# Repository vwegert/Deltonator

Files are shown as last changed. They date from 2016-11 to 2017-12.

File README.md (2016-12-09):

# CAUTION - WORK IN PROGRESS

If you happen to read this, beware - this has not been validated or tried out yet. So far, it is only a theoretical model.

# The Deltonator

You might also call it YAFDP - yet another f-word delta printer. It's a machine based on the linear delta kinematic
system like the famous [Rostock](http://reprap.org/wiki/Rostock) or [Kossel](http://reprap.org/wiki/Kossel). 

<a href="http://www.youtube.com/watch?feature=player_embedded&v=K8tiYmS-2c0" target="_blank">Deltonator Movement Simulation</a>

## Design Goals

When  setting out to build my own delta printer, I didn't find exactly what I was looking for, so - like many other 
people, many of which have considerable more experience than I have - I decided to design my own version, with the 
following design goals in mind:

 * Use the [MakerSlide](https://www.inventables.com/technologies/makerslide) system with V-shaped wheels for the 
   vertical axes.
 * Use a magnetic bearing system somewhat similar to the one designed by [Bert Broeren](http://www.thingiverse.com/thing:1239984), 
   that is, the magnets do not have to hold the weight of the effector.
 * Keep the effectors easily exchangeable to support different tool heads - various 3D printing heads, maybe a small 
   motor for PCB milling or a laser engraving module at some time.
 * Create an enclosed build volumes - for stable printing conditions, to prevent chips from flying all over the place 
   when milling and to contain the fumes when laser engraving.
 * Create a parametric design to be able to determine (and change) the sizes of key parts later on.
 * Keep the entire design open source, and use FOSS wherever possible.

At the current stage, the plans are incomplete and unproven, and any input is welcome. 

## OpenSCAD coding conventions

* global constants in UPPERCASE
* modules and functions lower_case_with_underscores
* things that are intended to be kept local begin with an _underscore

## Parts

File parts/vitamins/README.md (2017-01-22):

# Vitamins

This directory contains the files that produce parts that will have to be bought ready-made to prepare the printer.

## Bearings

Some of the bearings come from an extended version of the MCAD library, others are pre-generated from local 
instructions.

## GT2 pulleys

## Nuts

## Screws

The screws are pre-generated using the nutsnbolts library. Since that library (or any library) might not stay stable,
the repository contains the pre-rendered STL files.

## Stepper Motors

The motors are pre-generated using the MCAD library. Since that library (or any library) might not stay stable,
the repository contains the pre-rendered STL files.

## Switches

The SS-5GL switch model was downloaded from the [Omron Web Site](https://www.omron.com/ecb/products/sw/12/ss.html) and
then converted from STEP to STL manually using FreeCAD.

## V-Wheel

The file vwheel_b17021_rev_3.pdf was downloaded directly from the 
[buildlog site](http://www.buildlog.net/documents/b17021_rev_3.pdf). As far as I can tell from the PDF file, this file
has been licensed under a CC-BY-SA-3.0 license, but I have not been able to determine the actual author. Please 
contact me if you have details.

## Washers

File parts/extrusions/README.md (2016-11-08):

# Extrusions

This directory contains the files that are necessary to preoduce the extruded parts that are used for the printer frame.

## MakerSlide 

### own source files

* makerslide.scad contains some general functions that provide the dimensions of the profile as well as the modules used to import the rendered rails. This file is intended to be included by other files down the line.
* makerslide_rail.scad is used to render the actual rail into an STL file for faster access. This file is NOT intended to be included by any other file than makerslide.scad.

### files imported from external sources

Files:
* makerslide_b17022.dxf (original file name: b17022.dxf)
* makerslide_b17022_rev_2.pdf (original file name: b17022_rev_2.pdf)

These files were downloaded from [this repository](https://workbench.grabcad.com/workbench/projects/gcq_crZz-TsvjDvMKhmbtlfzNRmpeNJLO8d-8o69N-S1JA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), which in turn was linked from [the Inventables site](https://www.inventables.com/technologies/makerslide). As far as I can tell from the PDF file, these files have been licensed under a CC-BY-SA-3.0 license, but I have not been able to determine the actual author. Please contact me if you have details.

Files: 
* makerslide_extrusion_profile.dxf

Since the original extrusion profile was using non-standard dimensions and contained a considerable offset, I'm actually using a version by [mesheldrake](http://www.thingiverse.com/mesheldrake) downloaded from [Thingiverse](http://www.thingiverse.com/thing:8992). This file has been placed under a CC-BY-SA-3.0 license as well.

## OpenBuilds V-Slot 20x20 mm

### own source files

* vslot_2020.scad contains some general functions that provide the dimensions of the profile as well as the modules used to import the rendered rails. This file is intended to be included by other files down the line.
* vslot_2020_side.scad is used to render the actual side extrusion into an STL file for faster access. This file is NOT intended to be included by any other file than vslot_2020.scad.

### file simported from external sources

Files: 
* vslot_2020_fullscale.dxf (original file name: V-slot_2020_fullscale.dxd)

These files were downloaded from [the OpenBuilds website](http://www.openbuilds.com/projectresources/v-slot-extrusion-20x20-dxf.64/).

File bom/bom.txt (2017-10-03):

===== Aluminium Extrusions ============================================================

90° Corner Bracket for 2020 Extrusions
  ................................................................................ 6
    horizontal_assembly                                                      (6)

MakerSlide Extrusion
  800 mm.......................................................................... 3
    vertical_axis_assembly                                                   (3)

V-Slot Extrusion
  400x20x20 mm.................................................................... 9
    horizontal_assembly                                                      (9)

===== Bearings and Wheels =============================================================

Ball Bearing
  625RS........................................................................... 18
    vertical_axis_assembly >> carriage_hardware >> vslot_wheel               (18)
  F623............................................................................ 6
    vertical_axis_assembly >> tensioner_hardware                             (6)

Eccentric Spacer for V-Wheel
  ................................................................................ 3
    vertical_axis_assembly >> carriage_hardware                              (3)

V-Wheel for MakerSlide
  ................................................................................ 9
    vertical_axis_assembly >> carriage_hardware                              (9)

===== Electronic Components ===========================================================

Axial Fan
  25x25x10 mm..................................................................... 2
    effector_e3d_v6lite_hardware                                             (2)

End Switch
  SS-5GL.......................................................................... 3
    vertical_axis_assembly >> end_switch_bracket_hardware                    (3)

Escher IR Height Sensor
  Mini............................................................................ 1
    effector_e3d_v6lite_hardware >> ir_sensor_housing_hardware               (1)

Stepper Motor
  NEMA 17 medium.................................................................. 3
    vertical_axis_assembly >> motor_bracket_stepper                          (3)

===== General Hardware ================================================================

Flat Head Countersunk Socket Cap Screw (DIN 7991 / ISO 10642)
  M4 x 35 mm...................................................................... 3
    horizontal_assembly                                                      (3)

Hex Nut (DIN 934 / ISO 4032)
  M3.............................................................................. 6
    vertical_axis_assembly >> tensioner_hardware                             (6)
  M4.............................................................................. 21
    horizontal_assembly                                                      (6)
    horizontal_assembly >> enclosure_side_bracket_hardware                   (12)
    vertical_axis_assembly >> tensioner_hardware                             (3)
  M5.............................................................................. 9
    vertical_axis_assembly >> carriage_hardware                              (9)

Hex Socket Head Cap Screw (DIN 912 / ISO 4762)
  M2 x 10 mm...................................................................... 6
    vertical_axis_assembly >> end_switch_bracket_hardware >> screw           (6)
  M3 x 25 mm...................................................................... 3
    vertical_axis_assembly >> tensioner_hardware >> screw                    (3)
  M3 x 30 mm...................................................................... 3
    vertical_axis_assembly >> end_switch_bracket_hardware >> screw           (3)
  M3 x 6 mm....................................................................... 12
    vertical_axis_assembly >> motor_bracket_stepper_hardware >> screw        (12)
  M3 x 8 mm....................................................................... 8
    effector_e3d_v6lite_hardware >> ir_sensor_housing_hardware >> screw      (2)
    vertical_axis_assembly >> carriage_hardware >> screw                     (6)
  M4 x 10 mm...................................................................... 3
    horizontal_assembly >> screw                                             (3)
  M4 x 12 mm...................................................................... 48
    horizontal_assembly >> enclosure_side_bracket_hardware >> screw          (24)
    vertical_axis_assembly >> bed_bracket_hardware >> screw                  (6)
    vertical_axis_assembly >> foot_rail_hardware >> screw                    (6)
    vertical_axis_assembly >> head_hardware >> screw                         (6)
    vertical_axis_assembly >> motor_bracket_hardware >> screw                (6)
  M4 x 20 mm...................................................................... 30
    horizontal_assembly >> enclosure_long_side_plate_hardware >> screw       (12)
    vertical_axis_assembly >> enclosure_short_side_plate_hardware >> screw   (18)
  M4 x 25 mm...................................................................... 3
    vertical_axis_assembly >> tensioner_hardware >> screw                    (3)
  M4 x 8 mm....................................................................... 21
    horizontal_assembly >> screw                                             (3)
    vertical_axis_assembly >> bed_bracket_hardware >> screw                  (6)
    vertical_axis_assembly >> foot_rail_hardware >> screw                    (6)
    vertical_axis_assembly >> head_hardware >> screw                         (6)
  M5 x 25 mm...................................................................... 6
    vertical_axis_assembly >> carriage_hardware >> screw                     (6)
  M5 x 35 mm...................................................................... 3
    vertical_axis_assembly >> carriage_hardware >> screw                     (3)
  M8 x 30 mm...................................................................... 3
    vertical_axis_assembly >> foot_plate_hardware >> screw                   (3)

Large Washer (DIN 9021 / ISO 7093)
  M3.............................................................................. 6
    vertical_axis_assembly >> carriage_hardware                              (6)

Spring
  5x20 mm......................................................................... 6
    horizontal_assembly                                                      (3)
    vertical_axis_assembly >> end_switch_bracket_hardware                    (3)

T-Slot Nut
  M4.............................................................................. 75
    horizontal_assembly                                                      (3)
    horizontal_assembly >> enclosure_long_side_plate_hardware                (12)
    vertical_axis_assembly >> bed_bracket_hardware                           (12)
    vertical_axis_assembly >> enclosure_short_side_plate_hardware            (18)
    vertical_axis_assembly >> foot_rail_hardware                             (12)
    vertical_axis_assembly >> head_hardware                                  (12)
    vertical_axis_assembly >> motor_bracket_hardware                         (6)

Washer (DIN 125A / ISO 7089)
  M3.............................................................................. 30
    vertical_axis_assembly >> end_switch_bracket_hardware                    (3)
    vertical_axis_assembly >> motor_bracket_stepper_hardware                 (12)
    vertical_axis_assembly >> tensioner_hardware                             (15)
  M4.............................................................................. 117
    horizontal_assembly                                                      (18)
    horizontal_assembly >> enclosure_long_side_plate_hardware                (12)
    horizontal_assembly >> enclosure_side_bracket_hardware                   (24)
    vertical_axis_assembly >> bed_bracket_hardware                           (12)
    vertical_axis_assembly >> enclosure_short_side_plate_hardware            (18)
    vertical_axis_assembly >> foot_rail_hardware                             (12)
    vertical_axis_assembly >> head_hardware                                  (12)
    vertical_axis_assembly >> motor_bracket_hardware                         (6)
    vertical_axis_assembly >> tensioner_hardware                             (3)
  M5.............................................................................. 27
    vertical_axis_assembly >> carriage_hardware                              (27)

===== Printed Parts ===================================================================

Arm
  Carriage........................................................................ 3
    vertical_axis_assembly                                                   (3)

Effector
  E3D V6 Lite (Base Plate)........................................................ 1
                                                                             (1)
  E3D V6 Lite Spacer.............................................................. 2
    effector_e3d_v6lite_hardware                                             (2)

Enclosure
  Side Bracket.................................................................... 12
    horizontal_assembly                                                      (12)

Frame
  Bed Bracket..................................................................... 3
    vertical_axis_assembly                                                   (3)
  Foot (Rail Version)............................................................. 3
    vertical_axis_assembly                                                   (3)
  Foot Plate...................................................................... 3
    vertical_axis_assembly                                                   (3)
  Head............................................................................ 3
    vertical_axis_assembly                                                   (3)
  Motor Bracket................................................................... 3
    vertical_axis_assembly                                                   (3)

Small Parts
  Belt Tensioner.................................................................. 3
    vertical_axis_assembly                                                   (3)
  Bottom Magnet Holder............................................................ 6
    vertical_axis_assembly                                                   (6)
  End Switch Bracket.............................................................. 3
    vertical_axis_assembly                                                   (3)
  IR Sensor Housing............................................................... 1
    effector_e3d_v6lite_hardware                                             (1)
  Top Magnet Holder............................................................... 6
    vertical_axis_assembly                                                   (6)

===== Sheet / Cast Aluminium ==========================================================

Bed Plate
  d = 300 mm, h = 4 mm............................................................ 1
                                                                             (1)

===== Sheet / Multiplex Plywood =======================================================

Enclosure Door: Inner Horizontal Plate
  [3, 409, 56].................................................................... 2
    horizontal_assembly >> front_door_assembly                               (2)

Enclosure Door: Inner Vertical Plate
  [3, 29, 700].................................................................... 2
    horizontal_assembly >> front_door_assembly                               (2)

Enclosure Door: Outer Horizontal Plate
  [3, 320, 71.5].................................................................. 2
    horizontal_assembly >> front_door_assembly                               (2)

Enclosure Door: Outer Vertical Plate
  [3, 44.5, 813].................................................................. 2
    horizontal_assembly >> front_door_assembly                               (2)

Enclosure Long Side Plate
  411 x 800 x 6.5  mm............................................................. 2
    horizontal_assembly                                                      (2)

Enclosure Short Side Plate
  155 x 800 x 6.5  mm............................................................. 3
    vertical_axis_assembly                                                   (3)

===== Special Mechanic Parts ==========================================================

Carbon Fiber Rods
  330 mm, OD 8 mm, ID 0........................................................... 6
    vertical_axis_assembly                                                   (6)

Cylindrical Magnet
  d = 6 mm, h = 3 mm.............................................................. 2
    effector_e3d_v6lite_hardware >> ir_sensor_housing_hardware               (2)

Magnet Ring
  10x5 mm, bore 3.4 mm, 90° bevel with 7 mm diameter............................. 12
    vertical_axis_assembly >> magnet_holder_carriage_hardware                (6)
    vertical_axis_assembly >> magnet_holder_effector_hardware                (6)

Steel Ball
  10 mm diameter.................................................................. 12
    effector_e3d_v6lite_hardware >> effector_base_hardware                   (6)
    vertical_axis_assembly >> carriage_hardware                              (6)

===== Timing Belts and Pulleys ========================================================

GT2 Belt
  approx. 1504.82 mm.............................................................. 3
    vertical_axis_assembly                                                   (3)

GT2 Pulley
  20 Teeth x 5 mm Bore............................................................ 3
    vertical_axis_assembly >> motor_bracket_stepper                          (3)

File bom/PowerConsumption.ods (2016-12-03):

Pos. | Item |  | Current | Quantity | Combined
1 | Hotend Heater Cartridge | 40,0 W | 1,7 A | 3 | 5,0 A
2 | Extruder Stepper Motors |  | 0,2 A | 3 | 0,6 A
 | Rated Voltage | 2,55 V
 | Rated Current | 1,20 A
 | Additional Safety Factor | 50%
3 | Carriage Stepper Motors |  | 0,2 A | 3 | 0,6 A
 | Rated Voltage | 2,55 V
 | Rated Current | 1,20 A
 | Additional Safety Factor | 50%
4 | Extruder Fans | 4,0 W | 0,2 A | 2 | 0,3 A
5 | Part Cooling Fan | 6,0 W | 0,3 A | 1 | 0,3 A
6 | Electronics Fan | 5,0 W | 0,2 A | 2 | 0,4 A
7 | PanelDue | 3,5 W | 0,1 A | 1 | 0,1 A
8 | DuetWifi | 5,0 W | 0,2 A | 1 | 0,2 A
9
10
11
12
13
14
15
16
17
18
19
20
 | Subtotal |  |  |  | 7,5 A
 | Bed Heater | Diameter |  | 300 mm
 |  | Surface Area |  | 707 cm²
 |  | Power Factor |  | 0,4 W/cm²
 |  | Power |  | 282,7 W
 |  | Heater Current |  |  | 11,8 A
 | Spindle Motor |  | Power | 300,0 W
 |  |  | Motor Current |  | 12,5 A
 | Total Current |  |  |  | 20,0 A
 | Voltage |  | 24 V
 | Total Power |  |  |  |  | 480 W

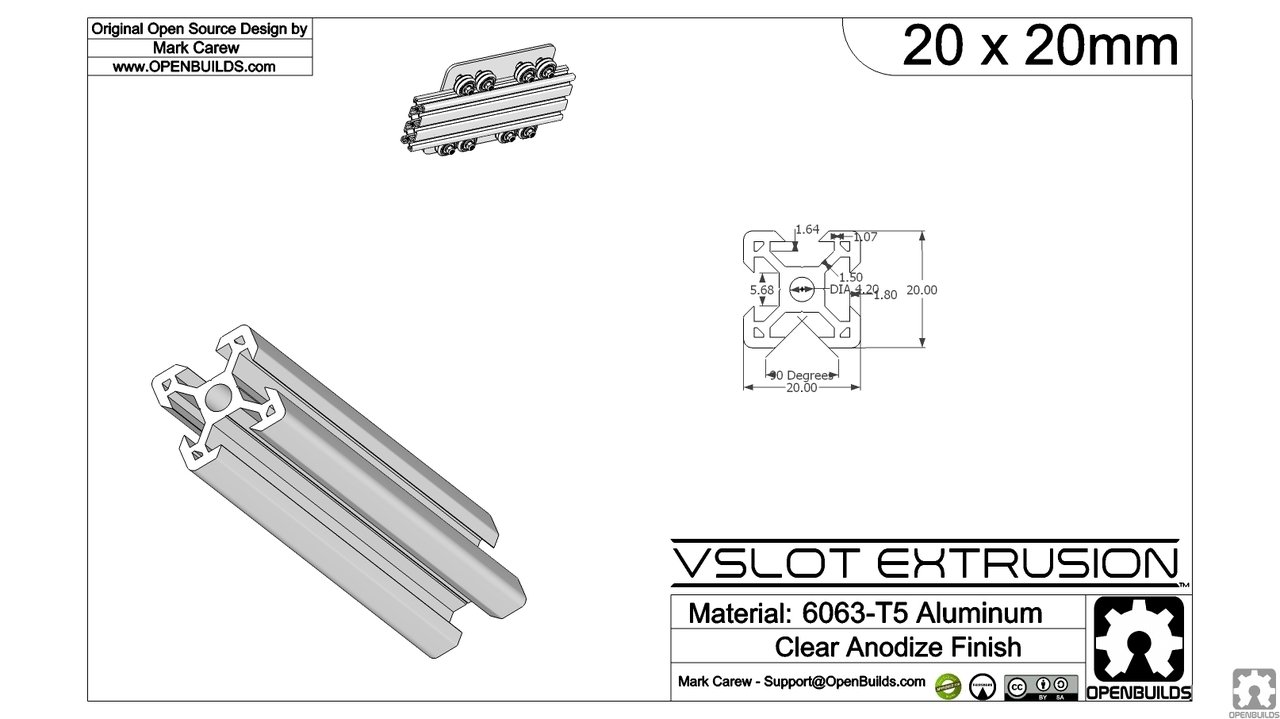
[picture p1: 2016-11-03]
parts/extrusions/vslot_2020_dimensions.jpg

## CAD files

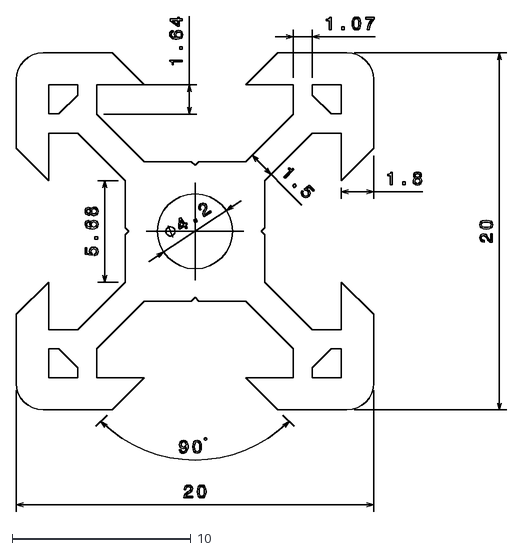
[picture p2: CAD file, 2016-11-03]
parts/extrusions/vslot_2020_fullscale.dxf
27.4 x 27.8

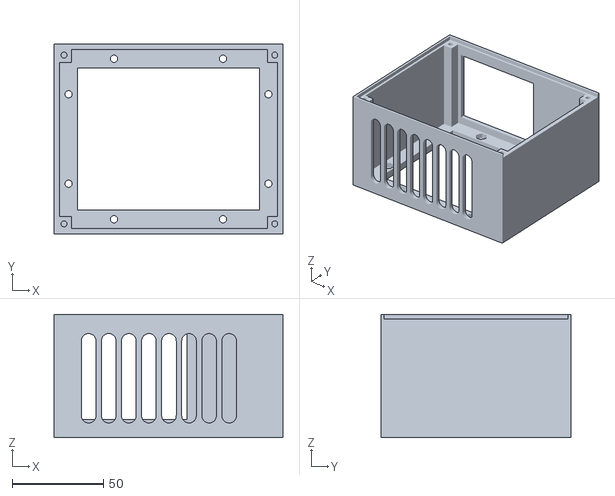
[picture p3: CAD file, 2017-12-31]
parts/printed/duet_holder.stl
125.5 x 104.0 x 67.5

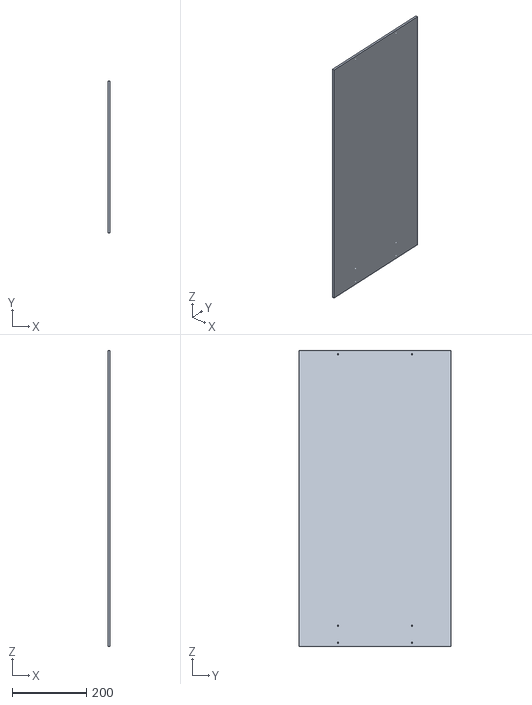
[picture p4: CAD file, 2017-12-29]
parts/sheets/enclosure_long_side.stl
6.50 x 411.0 x 800.0

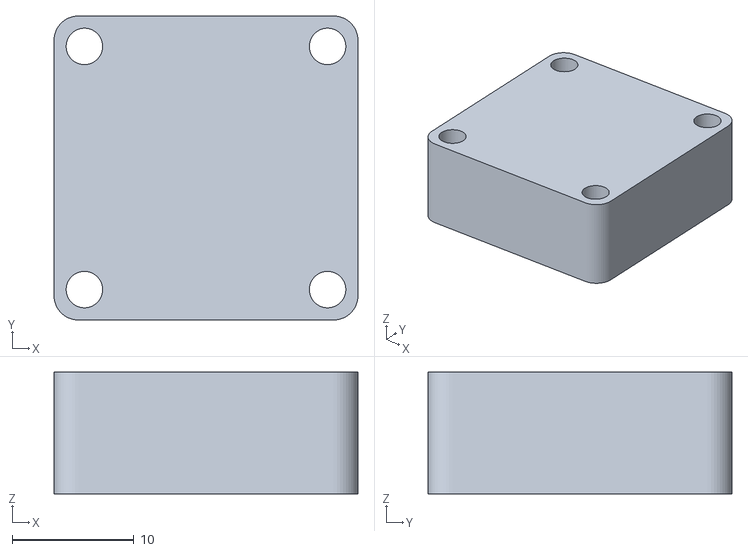
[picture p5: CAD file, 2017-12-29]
parts/vitamins/electromechanic/fan_axial_pc.stl
25.0 x 25.0 x 10.0

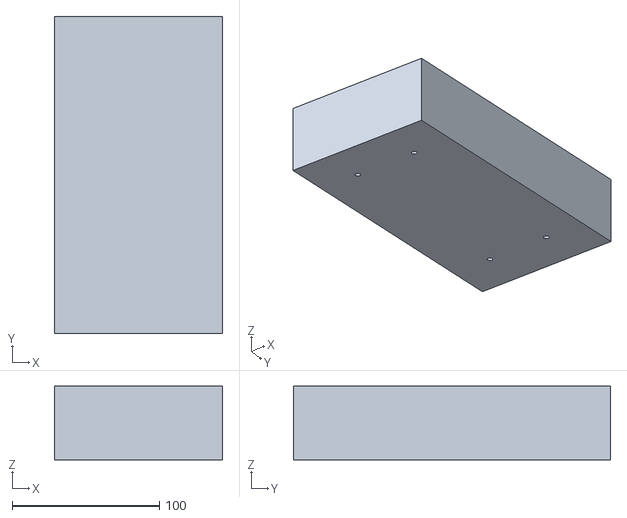
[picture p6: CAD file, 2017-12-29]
parts/vitamins/electronic/power_supply.stl
114.0 x 215.0 x 50.0

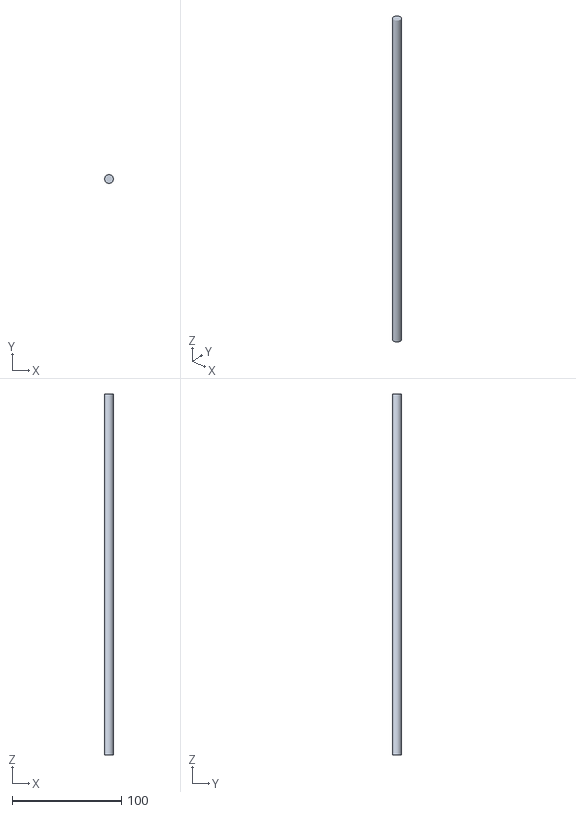
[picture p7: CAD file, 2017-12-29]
parts/vitamins/mechanic/rod.stl
8.00 x 8.00 x 330.0

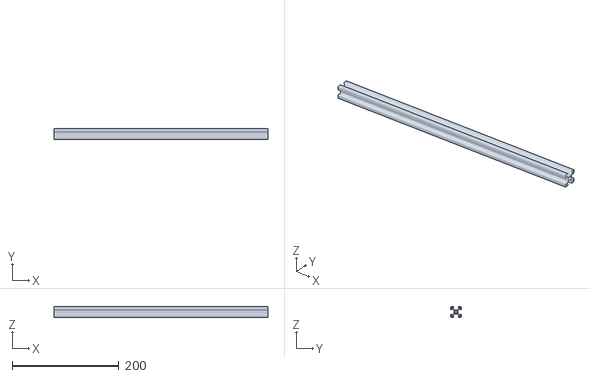
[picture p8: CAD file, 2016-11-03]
parts/extrusions/vslot_2020_side.stl
400.0 x 20.0 x 20.0

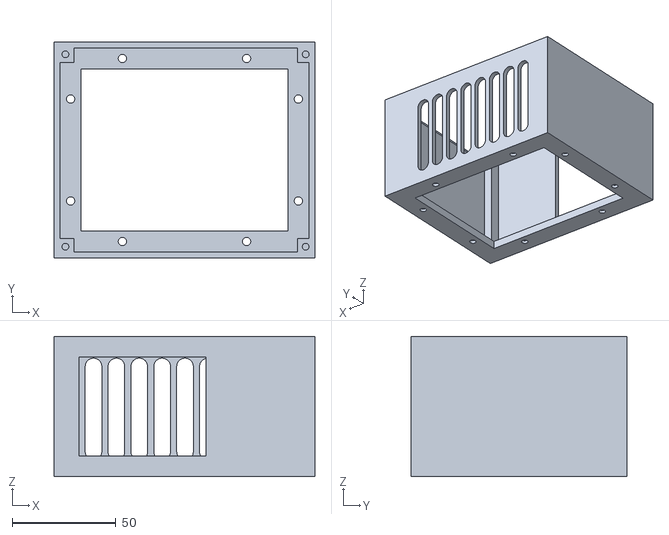
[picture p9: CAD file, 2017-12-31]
parts/printed/duetx_holder.stl
125.5 x 104.0 x 67.5

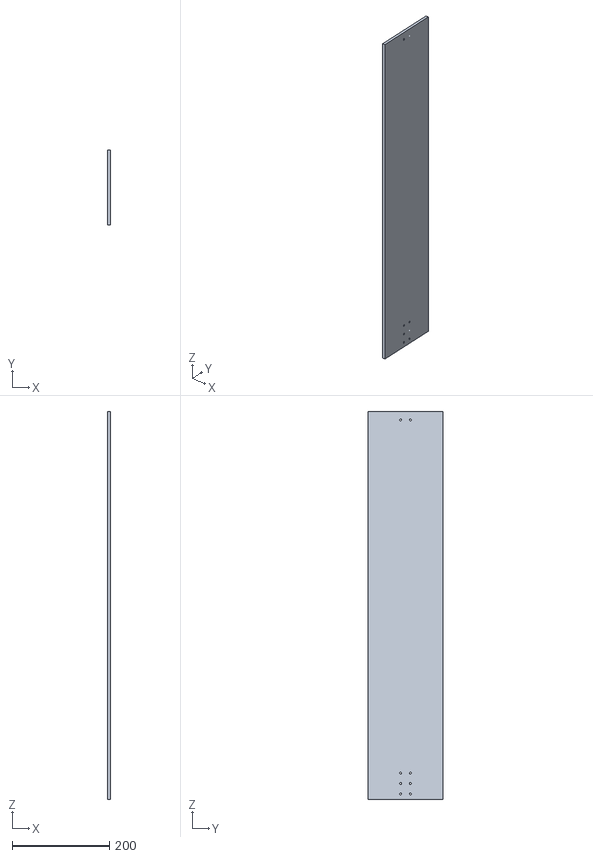
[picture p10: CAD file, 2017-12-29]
parts/sheets/enclosure_short_side.stl
6.50 x 155.0 x 800.0

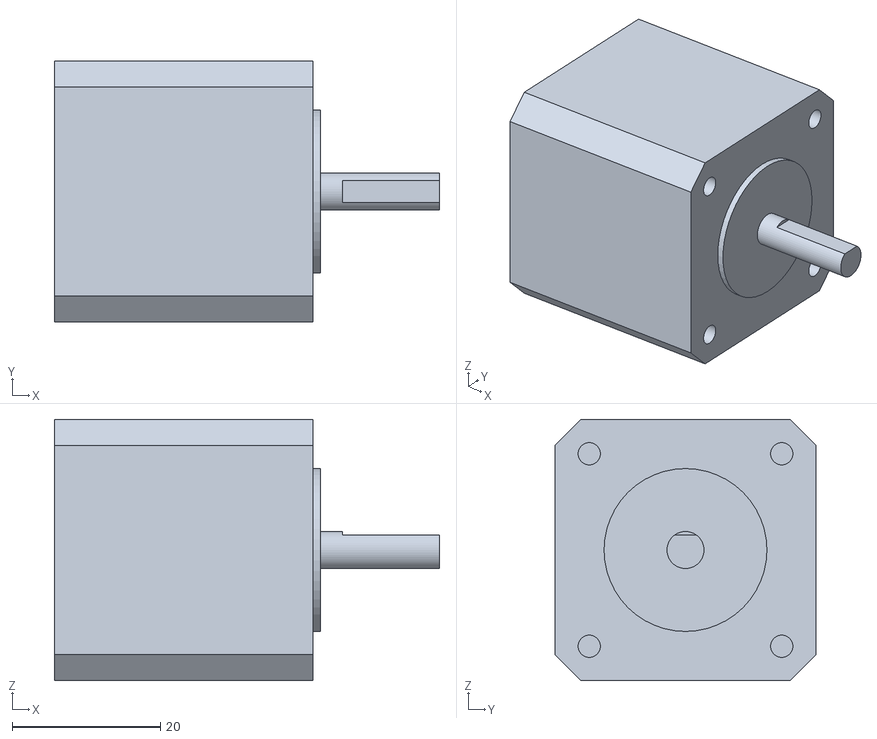
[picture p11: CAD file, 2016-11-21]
parts/vitamins/electromechanic/stepper_nema14_long.stl
52.0 x 35.3 x 35.3

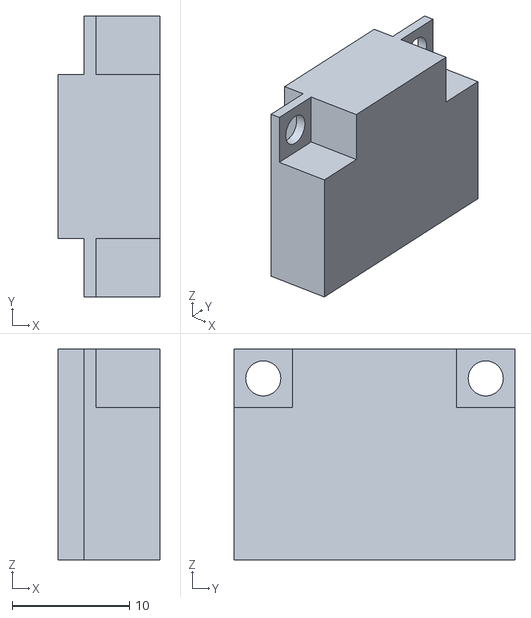
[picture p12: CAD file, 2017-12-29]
parts/vitamins/electronic/escher_ir_sensor.stl
8.75 x 24.0 x 18.0

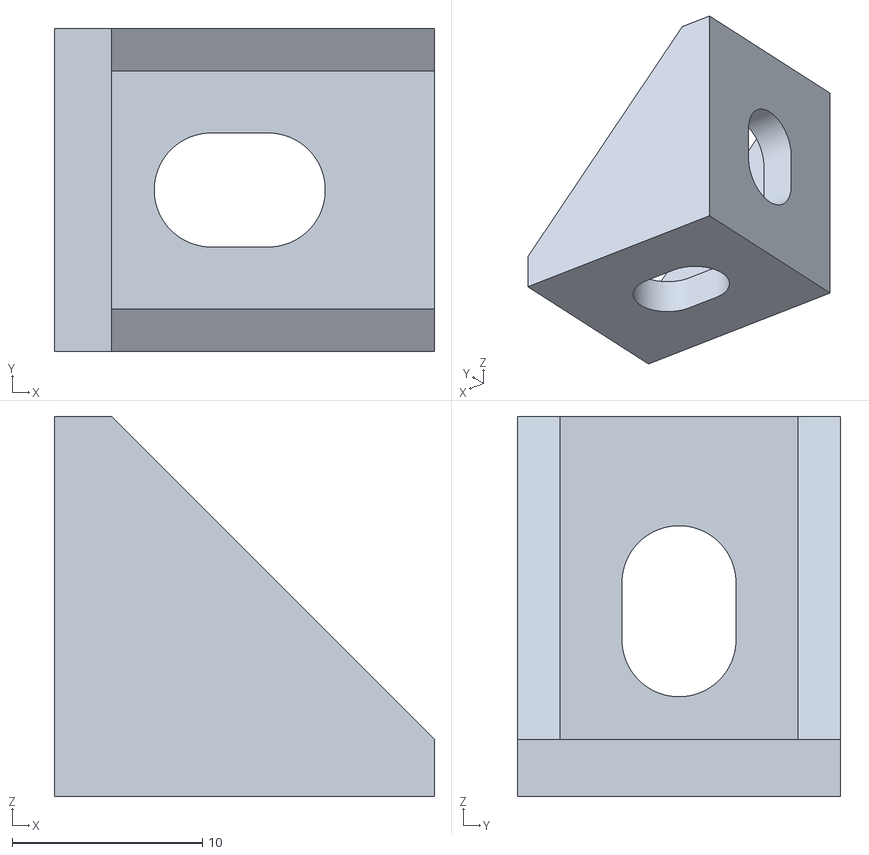
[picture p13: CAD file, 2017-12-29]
parts/vitamins/mechanic/rail_bracket.stl
20.0 x 17.0 x 20.0

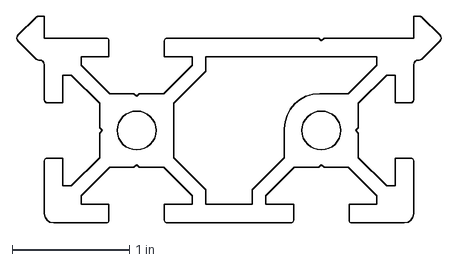
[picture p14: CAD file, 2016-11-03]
parts/extrusions/makerslide_b17022.dxf
3.62 x 1.76 in

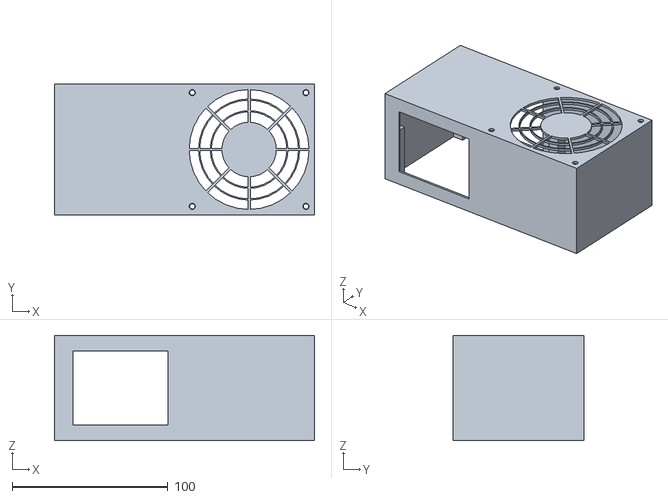
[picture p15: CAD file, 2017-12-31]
parts/printed/duet_fan_holder.stl
167.0 x 84.0 x 67.5

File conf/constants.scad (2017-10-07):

/**********************************************************************************************************************
 **
 ** conf/constants.scad
 **
 ** This file contains constants and aliases used for the part size definitions.
 **
 **********************************************************************************************************************/

/**
 * The alias names for the rails.
 * A is the "front left" rail, B the "front right" rail, C the back rail.
 * These constants are also used for the sides of the frame and the effector; in this case, side A is the one 
 * opposing rail A.
 */
A = 0;
B = 1;
C = 2;

/**
 * Aliases for metric screw/nut sizes.
 */
M2 = 2;
M3 = 3;
M4 = 4;
M5 = 5;
M8 = 8;

/** 
 * Aliases for NEMA stepper motors.
 */
NEMA14 = 14;
NEMA17 = 17;
NEMA23 = 23;

/**
 * The various types of effector heads supported.
 */
EFFECTOR_DUMMY      = 0;
EFFECTOR_E3D_V6LITE = 1;

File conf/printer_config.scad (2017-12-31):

/**********************************************************************************************************************
 **
 ** conf/printer_config.scad
 **
 ** This file contains the main control variables that determine the size and shape of the printer. Note that in the
 ** actual parts specifications, the constants defined here will only ever be accessed through functions defined in
 ** conf/derived_sizes.scad exclusively to allow for easier adaptation, should the mode of calculation change. 
 **
 ** All sizes in mm. Caution: Little to no cross-checking is implemented. Change values sensibly and one at a time.
 **
 ** This file is NOT to be included by any other file except for conf/derived_sizes.scad.
 **
 **********************************************************************************************************************/

include <constants.scad>

// ===== FRAME RAIL DIMENSIONS ========================================================================================

// The length of the vertical MakerSlide extrusions that make up the rails for the carriages.
FRAME_V_RAIL_HEIGHT = 800;

// The length of the horizontal 20x20 V-Slot extrusions that form the sides of the triangle.
FRAME_H_RAIL_LENGTH = 400;

// ===== WORKING SURFACE (BED) DIMENSIONS =============================================================================

// The thickness of the plate that serves as the heated bed.
BED_THICKNESS = 4;

// The diameter of the plate that serves as the heated bed.
BED_DIAMETER = 300;

// ===== DIMENSIONS OF THE PRINTED FRAME PARTS ========================================================================

// The additional clearance to leave around the MakerSlide extrusion.
MAKERSLIDE_CLEARANCE = 0.25;

// The thickness of the walls outside the extruded parts.
FRAME_PART_WALL_THICKNESS = 3;

// The thickness of the wall that separates the vertical rails from the horizontal extrusions.
FRAME_V_H_RAIL_SEPARATION = 8;

// The depth of the holes that hold the V-Slot extrusions.
FRAME_PART_VSLOT_DEPTH = 30;

// Whether to use a horizontal rail at the base of the printer or not.
FRAME_HORIZONTAL_BASE_RAIL = true;

// The depth of the holes in the foot that hold the MakerSlide extrusions. This is for the foot version that holds
// a horizontal rail.
FRAME_FOOT_RAIL_MAKERSLIDE_DEPTH = 23; 

// The depth of the plate in the foot that the external foot will screw into.
FRAME_FOOT_RAIL_PLATE_DEPTH = 15;

// The thickness of the plate in the foot that the external foot will screw into.
// Hint: Easier to print (although more material is required) if equals to FRAME_FOOT_RAIL_MAKERSLIDE_DEPTH.
FRAME_FOOT_RAIL_PLATE_HEIGHT = 23;

// The depth of the holes in the foot that hold the MakerSlide extrusions. This is for the foot version that does not
// hold a horizontal rail.
FRAME_FOOT_NORAIL_MAKERSLIDE_DEPTH = 17.5; 

// The size of the screws that can be used to mount the foot to the underlying surface.
FRAME_FOOT_PLATE_SCREW_SIZE = M8;

// The clearance to leave around the screw head on all sides.
FRAME_FOOT_PLATE_SCREW_HEAD_CLEARANCE = 0.25;

// The diameter of the adjustable foot that screws into the foot bracket. 
// Note that the polygon is INscribed into this circumference.
FRAME_FOOT_PLATE_DIAMETER = 50;

// The number of sides to the adjustable foot that screws into the foot bracket.
FRAME_FOOT_PLATE_SIDES = 8;

// The thickness of the adjustable foot that screws into the foot bracket.
// Keep this larger than the head of the screw used to fix it, or you will run into trouble.
FRAME_FOOT_PLATE_THICKNESS = 6.5;

// The height of the bracket that holds the motor. WARNING: Increasing this might make it difficult to 
// turn the screws that hold the motor.
FRAME_MOTOR_BRACKET_HEIGHT = 20;

// The height of the bracket that holds the intermediate level with the working surface (print bed).
// Will be A LOT easier to print if equals to 2020 extrusion width + FRAME_PART_WALL_THICKNESS
FRAME_BED_BRACKET_HEIGHT = 23; 

// The depth of the holes in the head that hold the MakerSlide extrusions.
FRAME_HEAD_MAKERSLIDE_DEPTH = 35; 

// The clearance between the tensioner / bracket and its guide blocks on either side.
FRAME_HEAD_GUIDE_CLEARANCE = 0.5;

// ===== ENCLOSURE DIMENSIONS =========================================================================================

// The material thickness of the solid (back and side) enclosure walls.
ENCLOSURE_SOLID_THICKNESS = 6.5;

// The thickness of the insulation layer between the enclosure walls and the brackets they are mounted to.
ENCLOSURE_INSULATION_THICKNESS = 2;

// The gap between the horizontal extrusions and the enclosure side walls.
ENCLOSURE_SIDE_GAP = 40;

// The factor used to round down the enclosure plate widths.
ENCLOSURE_ROUND_DOWN_TO = 1;

// The thickness of the brackets that hold the outer enclosure walls.
ENCLOSURE_BRACKET_THICKNESS = 6;

// The width of the brackets that hold the outer enclosure walls, excluding the parts that bolt on to the 
// horizontal rails.
ENCLOSURE_BRACKET_WIDTH = 40;

// The size of the glass pane in the front door.
ENCLOSURE_GLASS_WIDTH = 350;
ENCLOSURE_GLASS_HEIGHT = 700;

// The size of the gap around the glass pane.
ENCLOSURE_GLASS_GAP_WIDTH = 1.0;

// The width of the bevel in the front door that holds the glass.
ENCLOSURE_GLASS_BEVEL_WIDTH = 15;

// The additional clearance on the sides of the front door to allow for the hinge to move.
ENCLOSURE_DOOR_SIDE_CLEARANCE = 2.0;

// The thickness of the material of the front door.
ENCLOSURE_DOOR_WOOD_THICKNESS = 3.0;
ENCLOSURE_DOOR_GLASS_THICKNESS = 1.8;

// ===== CARRIAGE DIMENSIONS ==========================================================================================

// The thickness of the carriage base plate. A thicker plate will make the carriage stiffer, but cost more
// material to print and take away space from the working area.
CARRIAGE_PLATE_THICKNESS = 6;

// The width of the border around the holes in the carriage base plate that hold the V-Wheels. 
CARRIAGE_PLATE_BORDER_WIDTH = 8;

// The upward angle of the ball holder on the carriage.
CARRIAGE_BALL_HOLDER_ANGLE = 10;

// ===== ARM DIMENSIONS AND PARAMETERS ================================================================================

// The distance between the rods that hold the effector.
ROD_DISTANCE = 65;

// The outer diameter of the rods.
ROD_OUTER_DIAMETER = 8;

// The inner diameter of the rods. Set to 0 if the rods are not hollow.
ROD_INNER_DIAMETER = 0;

// The additional clearance to leave between the rod and the holder.
ROD_CLEARANCE = 0.25;

// The thickness of the outer wall around the rod.
ROD_HOLDER_WALL_THICKNESS = 2.2;

// The depth of the insets that hold the rods.
ROD_HOLDER_DEPTH = 10;

// The size of the text on the outside of the rod holders.
ROD_HOLDER_TEXT_SIZE = 9;

// The depth of the text on the outside of the rod holders.
ROD_HOLDER_TEXT_DEPTH = 0.5;

// The minimum angle of the arms.
ROD_MIN_ANGLE = 18;

// The factor used to round up the rod length.
ROD_ROUND_UP_TO = 5;

// Set this to a positive value if you want the rods to have a fixed length (for example if you have pre-fabricated
// rods). Set this to a negative value to have the rod length calculated automatically.
ROD_FIXED_LENGTH = 330;

// The thickness of the magnet holder arms.
MAGNET_HOLDER_THICKNESS = 5;

// The additional clearance to leave around the magnet holder pin.
MAGNET_CLEARANCE = 0.025;

// ===== IR SENSOR DIMENSIONS AND PARAMETERS ==========================================================================

// The additional clearance to leave around the PCB.
IR_SENSOR_PCB_CLEARANCE = 0.25;

// The additional clearance to leave around the magnets.
IR_SENSOR_MAGNET_CLEARANCE = 0.2;

// The size of the screws used to adjust the IR sensor.
IR_SENSOR_ADJUSTMENT_SCREW_SIZE = M4;

// ===== EFFECTOR DIMENSIONS AND PARAMETERS ===========================================================================

// The additional distance between the magnets on the effector (not the rod distance - the other one :-)).
// This value is added to the minimum distance determined by the magnet size and wall thickness.
EFFECTOR_BALL_ADDITIONAL_DISTANCE = 15;

// The thickness of the effector plate.
EFFECTOR_THICKNESS = 4;

// The type of effector to use.
EFFECTOR_TYPE = EFFECTOR_E3D_V6LITE;

// The clearance in Z direction to leave beneath the effector plate.
EFFECTOR_Z_CLEARANCE = 30.0;

// ===== POWER DISTRIBUTION PARAMETERS ================================================================================

// The thickness of the cover walls.
POWER_WALL_THICKNESS = 1.5;

// The clearance between the inner and outer parts of the covers as well as between the covers.
POWER_CLEARANCE = 0.5;

// ===== ELECTRONICS MOUNTING PARAMETERS ==============================================================================

// The thickness of the cover walls.
ELECTRONICS_WALL_THICKNESS = 1.5;
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

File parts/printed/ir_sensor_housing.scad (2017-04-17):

/**********************************************************************************************************************
 **
 ** parts/printed/ir_sensor_housing.scad
 **
 ** This file constructs the housing for the Mini Differential IR height sensor board available from 
 ** http://www.escher3d.com/pages/order/products/product1.php
 **
 **********************************************************************************************************************/

include <../../conf/colors.scad>
include <../../conf/derived_sizes.scad>
include <../../conf/part_sizes.scad>

use <../../bom/bom.scad>
use <../../parts/vitamins/vitamins.scad>

/**
 * Renders the main body of the housing without the "wings" to fasten it.
 */
module _ir_sensor_housing_body() {

	difference() {
		union() {
			// the outer shape of the housing
			difference() {
				cube([escher_ir_sensor_housing_body_depth(),
					  escher_ir_sensor_housing_body_width(),
					  escher_ir_sensor_housing_body_height()]);
				translate([escher_ir_sensor_housing_wall_thickness(), escher_ir_sensor_housing_wall_thickness(), 0])
				cube([escher_ir_sensor_housing_body_depth() - 2 * escher_ir_sensor_housing_wall_thickness(),
					  escher_ir_sensor_housing_body_width() - 2 * escher_ir_sensor_housing_wall_thickness(),
					  escher_ir_sensor_housing_body_height()]);
			}
		
			// the "resting blocks" on the underside of the PCB
			translate([escher_ir_sensor_housing_wall_thickness(), 
				       escher_ir_sensor_housing_wall_thickness(), 
				       0])
				cube([escher_ir_sensor_housing_top_bottom_clearance() + escher_ir_sensor_pcb_max_pin_length(),
					  escher_ir_sensor_pcb_bottom_side_clearance(),
					  escher_ir_sensor_housing_body_height()]);
			translate([escher_ir_sensor_housing_wall_thickness(), 
				       escher_ir_sensor_housing_body_width() - escher_ir_sensor_housing_wall_thickness() - escher_ir_sensor_pcb_bottom_side_clearance(), 
				       0])
				cube([escher_ir_sensor_housing_top_bottom_clearance() + escher_ir_sensor_pcb_max_pin_length(),
					  escher_ir_sensor_pcb_bottom_side_clearance(),
					  escher_ir_sensor_housing_body_height()]);
		
			// the "mounting blocks" on the component side of the PCB
			_mounting_block_thickness = escher_ir_sensor_pcb_max_component_height() + 
			                            escher_ir_sensor_housing_top_bottom_clearance();
			_mounting_block_x_offset = escher_ir_sensor_housing_body_depth() - escher_ir_sensor_housing_wall_thickness() - _mounting_block_thickness;
			_mounting_block_height = escher_ir_sensor_housing_body_height() - ( escher_ir_sensor_pcb_height() - escher_ir_sensor_pcb_top_edge_clearance() );
			_mounting_block_z_offset = escher_ir_sensor_pcb_height() - escher_ir_sensor_pcb_top_edge_clearance();
			translate([_mounting_block_x_offset, 
				       escher_ir_sensor_housing_wall_thickness(), 
				       _mounting_block_z_offset])
				cube([_mounting_block_thickness,
					  escher_ir_sensor_pcb_top_edge_clearance(),
					  _mounting_block_height]);
			translate([_mounting_block_x_offset, 
					   escher_ir_sensor_housing_body_width() - escher_ir_sensor_housing_wall_thickness() - escher_ir_sensor_pcb_top_edge_clearance(), 
				       _mounting_block_z_offset])
				cube([_mounting_block_thickness,
					  escher_ir_sensor_pcb_top_edge_clearance(),
					  _mounting_block_height]);
		}

		// minus the screw holes
		translate([-epsilon(),
			       escher_ir_sensor_screw_y_offset(),
			       escher_ir_sensor_screw_z_offset()])
			rotate([0, 90, 0])
				cylinder(d = tap_base_diameter(escher_ir_sensor_hole_size()),
					     h = escher_ir_sensor_housing_body_depth() + 2 * epsilon(),
				    	 $fn = escher_ir_sensor_resolution());
		translate([-epsilon(),
			       escher_ir_sensor_housing_body_width() - escher_ir_sensor_screw_y_offset(),
			       escher_ir_sensor_screw_z_offset()])
			rotate([0, 90, 0])
				cylinder(d = tap_base_diameter(escher_ir_sensor_hole_size()),
					     h = escher_ir_sensor_housing_body_depth() + 2 * epsilon(),
				    	 $fn = escher_ir_sensor_resolution());
	}
}

/**
 * Renders the two "wings" that hold the magnets.
 */
module _ir_sensor_housing_magnet_holders() {

	// move to the Z base
	translate([0, 0, escher_ir_sensor_housing_body_height() - escher_ir_sensor_magnet_holder_height()]) {

		// create the left block
		translate([0, -escher_ir_sensor_magnet_holder_width(), 0]) 
			difference() {
				// the block
				cube([escher_ir_sensor_magnet_holder_depth(),
					  escher_ir_sensor_magnet_holder_width(),
					  escher_ir_sensor_magnet_holder_height()]);

				// minus the hole for the magnets
				translate([escher_ir_sensor_magnet_holder_depth() / 2,
					       escher_ir_sensor_housing_wall_thickness() + escher_ir_sensor_magnet_clearance() + escher_ir_sensor_magnet_diameter()/2,
					       escher_ir_sensor_magnet_holder_height() - (escher_ir_sensor_magnet_height() + escher_ir_sensor_magnet_clearance())])
				cylinder(d = escher_ir_sensor_magnet_diameter() + 2 * escher_ir_sensor_magnet_clearance(),
					     h = escher_ir_sensor_magnet_height() + escher_ir_sensor_magnet_clearance(),
					     $fn = escher_ir_sensor_resolution());
			}

		// create the right block
		translate([0, escher_ir_sensor_housing_body_width(), 0]) 
			difference() {
				// the block
				cube([escher_ir_sensor_magnet_holder_depth(),
					  escher_ir_sensor_magnet_holder_width(),
					  escher_ir_sensor_magnet_holder_height()]);

				// minus the hole for the magnets
				translate([escher_ir_sensor_magnet_holder_depth() / 2,
					       escher_ir_sensor_magnet_clearance() + escher_ir_sensor_magnet_diameter()/2,
					       escher_ir_sensor_magnet_holder_height() - (escher_ir_sensor_magnet_height() + escher_ir_sensor_magnet_clearance())])
				cylinder(d = escher_ir_sensor_magnet_diameter() + 2 * escher_ir_sensor_magnet_clearance(),
					     h = escher_ir_sensor_magnet_height() + escher_ir_sensor_magnet_clearance(),
					     $fn = escher_ir_sensor_resolution());
			}
	}
} 

/**
 * Creates the housing by rendering it from scratch. This module is not to be called externally, use 
 * ir_sensor_housing() instead.
 */
module _render_ir_sensor_housing() {
	color_printed_head_parts()
		render() {
			translate([-escher_ir_sensor_housing_body_depth() / 2,
				       -escher_ir_sensor_housing_body_width() / 2,
				       -escher_ir_sensor_housing_body_height()]) {
				_ir_sensor_housing_body();
				_ir_sensor_housing_magnet_holders();
			}
		} 
}

/**
 * Main module to use the pre-rendered sensor housing. 
 * The housing is centered on its base to facilitate mounting calculations.
 */
module ir_sensor_housing() {
	bom_entry(section = "Printed Parts", description = "Small Parts", size = "IR Sensor Housing");
	color_printed_head_parts()
		import(file = "ir_sensor_housing.stl");
}

/** 
 * Renders the hardware (nuts, bolts, screws) that are used to fixed the printed part to the surrounding parts.
 * This also includes the sensor board.
 */
module ir_sensor_housing_hardware() {

	translate([-escher_ir_sensor_housing_body_depth() / 2,
		       -escher_ir_sensor_housing_body_width() / 2,
		       -escher_ir_sensor_housing_body_height()]) {

		// the sensor board inside the housing
		translate([escher_ir_sensor_housing_wall_thickness() 
			       + escher_ir_sensor_housing_top_bottom_clearance()
    	           + escher_ir_sensor_pcb_max_pin_length()
    	           + escher_ir_sensor_housing_pcb_clearance(),
			       escher_ir_sensor_housing_wall_thickness() 
    	           + escher_ir_sensor_housing_pcb_clearance(),
			       0])
			escher_ir_sensor();
	
		// the screws to hold the sensor board
		translate([-epsilon(),
			       escher_ir_sensor_screw_y_offset(),
			       escher_ir_sensor_screw_z_offset()])
			screw(size = escher_ir_sensor_hole_size(),
				  min_length = escher_ir_sensor_screw_min_length(),
				  max_length = escher_ir_sensor_housing_body_depth());
		translate([-epsilon(),
			       escher_ir_sensor_housing_body_width() - escher_ir_sensor_screw_y_offset(),
			       escher_ir_sensor_screw_z_offset()])
			screw(size = escher_ir_sensor_hole_size(),
				  min_length = escher_ir_sensor_screw_min_length(),
				  max_length = escher_ir_sensor_housing_body_depth());
	
		// the magnets
		translate([escher_ir_sensor_magnet_holder_depth()/2,
			       - escher_ir_sensor_magnet_diameter() / 2 - escher_ir_sensor_magnet_clearance(), 
			       escher_ir_sensor_housing_body_height() - escher_ir_sensor_magnet_height()]) 
			magnet_cylinder();
		translate([escher_ir_sensor_magnet_holder_depth()/2,
			       escher_ir_sensor_housing_body_width() + escher_ir_sensor_magnet_diameter() / 2 + escher_ir_sensor_magnet_clearance(), 
			       escher_ir_sensor_housing_body_height() - escher_ir_sensor_magnet_height()]) 
			magnet_cylinder();

	}
}

_render_ir_sensor_housing();

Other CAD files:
parts/sheets/bed.stl
parts/vitamins/electromechanic/stepper_nema17_short.stl
parts/vitamins/electronic/duet_wifi_board.stl
parts/vitamins/mechanic/magnet_cylinder.stl
parts/printed/motor_bracket.scad
assemblies/extruder_plate.scad
assemblies/front_door.scad
assemblies/horizontal_right.scad
assemblies/horizontal_side.scad
assemblies/vertical_axis.scad
bom/bom.scad
conf/colors.scad
conf/derived_sizes.scad
conf/part_sizes.scad
parts/extrusions/makerslide.scad
parts/extrusions/makerslide_extrusion_profile.dxf
parts/extrusions/makerslide_rail.scad
parts/extrusions/makerslide_rail.stl
parts/extrusions/vslot_2020.scad
parts/extrusions/vslot_2020_side.scad
parts/printed/bed_bracket.scad
parts/printed/bed_bracket.stl
parts/printed/carriage.scad
parts/printed/carriage.stl
parts/printed/duet_common.scad
parts/printed/duet_fan_holder.scad
parts/printed/duet_holder.scad
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

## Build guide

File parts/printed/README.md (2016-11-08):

# Printed Parts

This directory contains the files that produce the parts that need to be printed (or IM'ed if thousands of orders 
should be placed, haha).

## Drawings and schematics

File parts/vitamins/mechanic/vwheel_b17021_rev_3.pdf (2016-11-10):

| REVISIONS

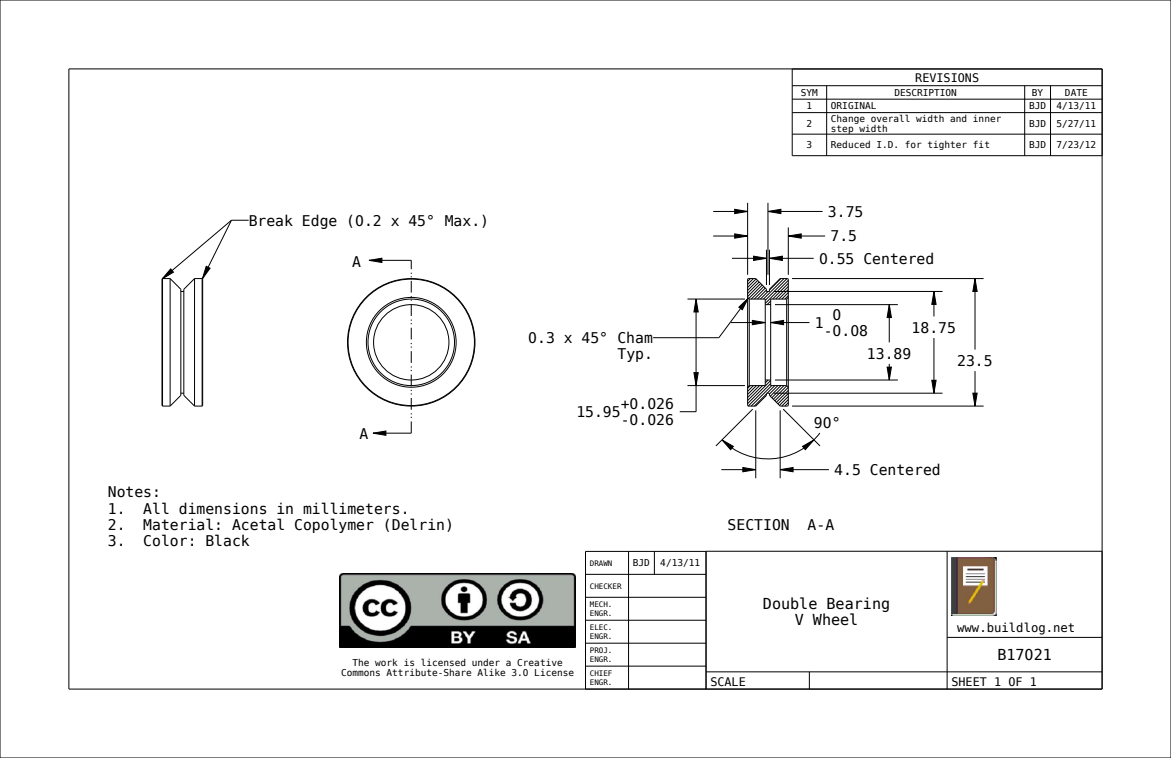
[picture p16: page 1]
0.55 Centered; 4.5 Centered; SECTION A-A; 0.3 x 45° Cham Typ.

SYM | DESCRIPTION | BY | DATE
1 | ORIGINAL | BJD | 4/13/11
2 | Change overall width and inner step width | BJD | 5/27/11

3 | Reduced I.D. for tighter fit | BJD | 7/23/12

Break Edge (0.2 x 45° Max.)

Notes:
1. All dimensions in millimeters.
2. Material: Acetal Copolymer (Delrin)
3. Color: Black

DRAWN | BJD | 4/13/11 | Double Bearing V Wheel | www.buildlog.net

CHECKER

MECH. ENGR.

ELEC. ENGR.

PROJ. ENGR.

The work is licensed under a Creative
Commons Attribute-Share Alike 3.0 License

CHIEF ENGR.

SCALE | SHEET 1 OF 1

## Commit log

2016-11-03 initial import of compile path with MakerSlide rail
    [colors.scad, derived_sizes.scad, makerslide.scad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]
2016-11-03 fixed color name
    [colors.scad]
2016-11-03 V-Slot 20x20 mm extrusions + basic build path for sides
    [derived_sizes.scad, horizontal_front.scad, horizontal_left.scad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]
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2016-11-06 fixed horizontal extrusion offset
    [vslot_2020_side.scad, vslot_2020_side.stl]
2016-11-06 rail distance calculation and side assembly placement
    [derived_sizes.scad, horizontal_front.scad, horizontal_left.scad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]
2016-11-06 added basic BOM generation
    [bom.scad, makerslide.scad, vslot_2020.scad]
2016-11-06 added printed part for frame foot
    [colors.scad, derived_sizes.scad, foot.scad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]
2016-11-06 added hardware for foot assembly
    [colors.scad, derived_sizes.scad, foot.scad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]
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2016-11-07 added pre-rendered stepper motors
    [colors.scad]
2016-11-07 fixed stepper motor alignment
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2016-11-07 fixed base screw collision
    [foot.scad, foot.stl]
2016-11-07 added vertical axis motor bracket
    [colors.scad, derived_sizes.scad, foot.stl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]
2016-11-07 introduced sections for BOM output
    [bom.scad, foot.scad, foot.stl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]
2016-11-08 submodule reorg, part 1
    [foot.scad, motor_bracket.scad, screw_M3x6.scad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]
2016-11-08 submodule reorg, part 2
    [screw_M3x6.stl, screw_M5x12.stl, screw_M5x8.stl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]
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2016-11-08 added GT2 pulleys to motors
    [colors.scad, derived_sizes.scad, foot.stl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]
2016-11-10 added provisional belt to vertical assembly
    [vertical_axis.scad]
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2016-11-10 added 625 bearing and extended V-Wheel module
    [bearing_625.scad, bearing_625.stl, bearings.scad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]
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2016-11-12 added eccentric spacer for V-Wheels
    [bearings.scad, part_sizes.scad, vwheel_spacer.scad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]
2016-11-12 added basic version of carriage
    [bearing_625.stl, carriage.scad, carriage.stl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]
2016-11-12 reversed belt mounting
    [carriage.stl, derived_sizes.scad, foot.stl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]
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2016-11-13 added belt holder to carriage
    [carriage.scad, carriage.stl, derived_sizes.scad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]
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2016-11-18 switched some dimensions to parameterized functions
    [carriage.scad, carriage.stl, derived_sizes.scad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]
2016-11-18 added F623ZZ ball bearing
    [bearing_f623.scad, bearing_f623.stl, carriage.stl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]
2016-11-18 fixed carriage color
    [carriage.scad, carriage.stl]
2016-11-18 added additional screw lengths
    [screw_M4x45.scad, screw_M4x45.stl, screw_M4x55.scad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]
2016-11-18 fixed bearing rendering resolution
    [bearing_f623.scad, bearing_f623.stl]
2016-11-18 added missing screw lengths, added nut_recess(size)
    [vitamins.scad]
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2016-11-18 changed frame / rail mounts from M5 to M4, added washers
    [carriage.stl, derived_sizes.scad, foot.scad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]
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2016-11-19 adjusted eccentric spacer dimensions
    [carriage.stl, foot.stl, motor_bracket.stl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]
2016-11-19 added model for Duet Wifi board
    [duet_wifi_board.stl]
2016-11-19 added basic version of frame head
    [carriage.stl, derived_sizes.scad, foot.scad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]
2016-11-20 integrated tensioner into head assembly, adjusted belt length
    [carriage.stl, derived_sizes.scad, foot.stl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]
2016-11-20 improved tensioner screw configuration and placement
    [carriage.stl, derived_sizes.scad, foot.stl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]
2016-11-20 added clearance for MakerSlide sleeves
    [carriage.stl, derived_sizes.scad, foot.stl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]
2016-11-20 added cutout to carriage to allow for greater Z range
    [carriage.scad, carriage.stl, derived_sizes.scad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]
2016-11-20 added basic version of end switch bracket
    [carriage.stl, colors.scad, derived_sizes.scad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]
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2016-11-21 added M2 and M3 components
    [bearing_625.scad, bearing_625.stl, nut_M2.scad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]
2016-11-21 completed end switch bracket assembly
    [carriage.stl, derived_sizes.scad, end_switch_bracket.scad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]
2016-11-21 made head/foot height independently configurable
    [carriage.stl, derived_sizes.scad, end_switch_bracket.stl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]
2016-11-21 added bed-level bracket and rails
    [bed_bracket.scad, bed_bracket.stl, carriage.stl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]
2016-11-22 added script to calculate the various sizes and output an overview file
    [bed_bracket.stl, carriage.stl, derived_sizes.scad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]
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2016-11-22 added first version of magnet holders
    [bed_bracket.stl, carriage.scad, carriage.stl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]
2016-11-23 adapted magnet holders on carriage
    [bed_bracket.stl, carriage.scad, carriage.stl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]
2016-11-23 added basic version of effector
    [bed_bracket.stl, carriage.stl, colors.scad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]
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2016-11-25 added clearance for magnet holder
    [bed_bracket.stl, carriage.stl, derived_sizes.scad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]
2016-11-26 differentiated between upper and lower magnet holder
    [bed_bracket.stl, carriage.stl, derived_sizes.scad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]
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2016-11-27 modified effector for ball mount on the underside
    [bed_bracket.stl, carriage.stl, carriage_ball_holder.stl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]
2016-11-27 resolved naming conflict
    [derived_sizes.scad, dump_sizes.scad, magnet_holder_carriage.scad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]
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2016-11-29 fixed positioning of rods on carriages
    [bed_bracket.stl, carriage.stl, carriage_ball_holder.scad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]
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2016-11-29 fixed angle calculation of arm C
    [derived_sizes.scad]
2016-11-29 added effector and dummy tool, adjusted arm min angle
    [bed_bracket.stl, carriage.stl, carriage_ball_holder.stl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]
2016-11-30 fixed effector ball holders, shortened lower magnet holders
    [bed_bracket.stl, carriage.stl, carriage_ball_holder.stl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]
2016-12-02 fixed arm rod positioning in the model
    [bed_bracket.stl, carriage.stl, carriage_ball_holder.stl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]
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2016-12-04 fixed bug in arm angle calculation
    [derived_sizes.scad]
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2016-12-04 renamed foot for later addition of an alternate version
    [foot_rail.scad, foot_rail.stl, vertical_axis.scad]
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2016-12-08 corrected arm length calculation
    [derived_sizes.scad, dump_sizes.scad, printer.scad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]
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2016-12-09 modified effector ball holders and adjusted arm angle/length
    [bed.stl, bed_bracket.stl, carriage.stl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]
2016-12-09 made rail screws conditional, removed about half of the screws
    [bed.stl, bed_bracket.scad, bed_bracket.stl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]
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2016-12-12 moved right-hand nut to the outside of the bracket
    [enclosure_side_bracket.scad, enclosure_side_bracket.stl]
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2016-12-12 fixed comments and part labels
    [enclosure_short_side.scad]
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2016-12-17 fixed typo
    [derived_sizes.scad, enclosure_side_bracket.scad]
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2016-12-21 fixed enclosure side calculations, added bevel
    [derived_sizes.scad, dump_sizes.scad, enclosure_long_side.stl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]
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2017-01-02 added mounting holes and hardware for long enclosure sides
    [derived_sizes.scad, dump_sizes.scad, enclosure_long_side.scad]
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2017-01-31 integrated ball holder into carriage, fixed hole sizes
    [bed.stl, bed_bracket.stl, carriage.scad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]
2017-02-01 added T-Slot nut holders, fixed missing hole in head bracket
    [bed_bracket.scad, foot_norail.scad, foot_rail.scad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]
2017-02-01 minor bug fixes
    [foot_rail.scad, vertical_axis.scad]
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2017-02-02 adjusted MakerSlide clearance
    [bed_bracket.stl, end_switch_bracket.stl, foot_norail.stl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]
2017-02-02 increased head guide clearances
    [bed_bracket.stl, derived_sizes.scad, end_switch_bracket.stl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]
2017-02-03 added screw fixation to rail foot
    [bed.stl, bed_bracket.stl, carriage.stl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]
2017-02-10 minor carriage corrections
    [bed.stl, bed_bracket.stl, carriage.scad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]
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2017-02-13 adjusted rod size, added labels to magnet holders
    [derived_sizes.scad, dump_sizes.scad, magnet_holder.scad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]
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2017-02-14 fixed IR housing dimensions
    [ir_sensor_housing.stl, printer_config.scad]
2017-03-11 added option to set fixed rod length
    [derived_sizes.scad, dump_sizes.scad, printer_config.scad]
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2017-04-17 adjusted effector Z clearance
    [bed.stl, bed_bracket.stl, carriage.stl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]
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2017-04-18 adjusted sheet sizes, added test model for some guesswork
    [bed.stl, bed_bracket.stl, carriage.stl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]
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2017-10-15 fixed hole and screw alignment
    [derived_sizes.scad, power_supply_base.scad, power_supply_cover.scad]
2017-10-15 fixed screw positioning
    [power_supply_base.scad]
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2017-12-31 added clearance around PCBs
    [derived_sizes.scad, duet_fan_holder.stl, duet_holder.scad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]
